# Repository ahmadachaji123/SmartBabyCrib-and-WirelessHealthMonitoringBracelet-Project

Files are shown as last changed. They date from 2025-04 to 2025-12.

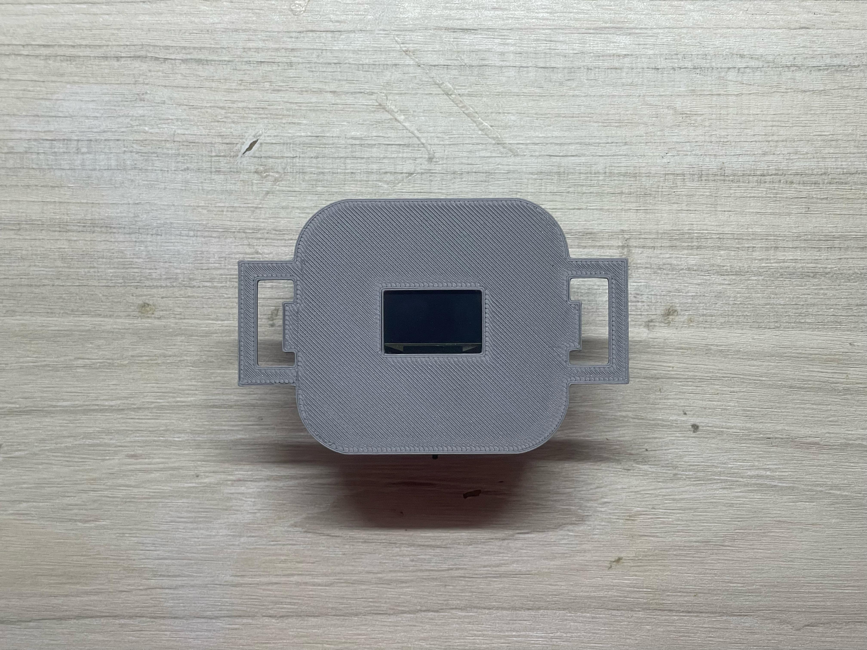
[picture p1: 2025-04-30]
Photo/design.jpg

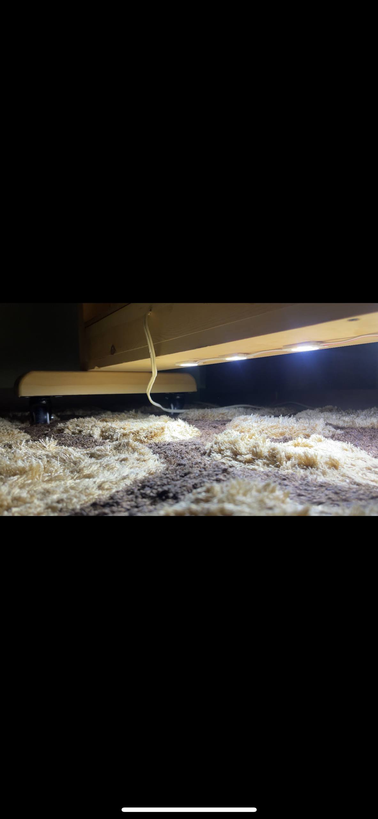
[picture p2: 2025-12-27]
Photo/photo_2025-12-27_20-52-59.jpg

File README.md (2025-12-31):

Smart Baby Crib – Final Year Project
A fully integrated Smart Baby Crib System developed as a Final Year Project in Mechatronics Engineering, focusing on baby safety, health monitoring, automation, and remote access.

🔹 Features
Wireless Health Monitoring: Heart rate, body temperature, and SpO₂ displayed on crib screen and mobile app
System Status: Bracelet battery, ambient temperature; humidity fixed at 70% (sensor damaged)
Remote Monitoring & Control: Mobile app connected via Wi-Fi to an online database, full control from anywhere
Synchronized Control: Swing, lights, music, system status updated in real time between crib and app
Auto Mode: Can be enabled/disabled from crib or phone; currently triggered by noise, planned upgrade to baby-cry detection
Health Data Visualization: 7-day real-time graphs (HR, temperature, SpO₂) on app or web browser; older data deleted automatically

🛠 Technologies
Embedded C/C++ for microcontrollers
Wireless sensors and communication modules
Mobile app & web dashboard for control and visualization
Mechanical design & structural analysis

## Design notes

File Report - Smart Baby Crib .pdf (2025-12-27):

1 | P a g e

## RAFIK HARIRI UNIVERSITY

## SMART BABY CRIB

Done by

## AHMAD ACHAJI

## AHMAD HAMMOUDEH

## SLEIMAN SMAILI

## ZIAD ZOK

Submitted to

## DR. Ahmad Koubeissi

This Senior Project is submitted in Partial Fulfillment of the Requirements of the BE Degree of

Mechatronics Engineering Major of the College of Engineering at Rafik Hariri University

## MECHREF-LEBANON

## April 2025

2 | P a g e

Copyright © 2024. All Rights Reserved

Ahmad Achaji (20210313)

Ahmad Hammoudeh (20210482)

Sleiman Smaili (20210629)

Ziad Zok (20210281)

3 | P a g e

## ACKNOWLEDGMENT

This project is the culmination of countless hours of collaboration, dedication, and a shared commitment to innovation in the development of our Smart Baby Crib. It stands as a reflection of the collective efforts of a passionate and determined team striving to bring technological advancements into the world of infant care.

First and foremost, we would like to express our profound gratitude to Dr. Ahmad Koubeissi, whose unwavering support, insightful feedback, and continuous encouragement were vital throughout every stage of this project. His guidance not only propelled our progress but also helped us maintain focus and purpose from inception to final execution.

We would also like to extend our sincere appreciation to the faculty of the Mechatronics Engineering Department at Rafik Hariri University, whose foundational teaching and support laid the groundwork for our academic and professional development. Their role in shaping our engineering mindset cannot be overstated.

To our friends, who offered both moral support and practical advice during the challenging phases, thank you for your uplifting words and clever solutions that helped us navigate tough situations with confidence.

Finally, and most importantly, we owe our deepest thanks to our families. Their boundless patience, love, and sacrifices, whether emotional, physical, or financial, were the pillars that carried us through this journey. Without their enduring belief in our potential, this achievement would not have been possible.

This Smart Baby Crib project is as much theirs as it is ours.

## ABSTRACT

This report presents the comprehensive design and development of a Smart Baby Crib, an innovative system aimed at enhancing infant care by integrating health monitoring, environmental control, and automated soothing mechanisms. The project scope involves the creation of a multifunctional crib that leverages IoT connectivity, real-time sensing, and embedded systems to ensure the baby’s comfort and safety while offering caregivers convenient remote access and control.

The Smart Baby Crib is equipped with vital health monitoring features, including temperature, heart rate, and oxygen level sensors, all wirelessly transmitted via a wearable bracelet. The system includes both manual and automatic operation modes, with automated rocking, music playback, and lighting control triggered by real-time sound detection and sensor feedback. Additionally, a heating and cooling subsystem is implemented using Peltier cells to regulate mattress temperature, ensuring a consistent sleep environment.

4 | P a g e

This report explores the mechanical, electrical, and embedded software design aspects of the crib, emphasizing safety, affordability, and user-friendliness. The project also addresses challenges related to data privacy, long-term operation, and system reliability, delivering a practical solution for modern-day parenting.

5 | P a g e

## TABLE OF CONTENTS

6 | P a g e
Crib ESP32 Code | 101
Crib Arduino Code | 124
Web Graphs code | 134
Mobile application | 148

LIST OF FIGURES

Figure 1: Cradle-Wise Smart Bassinet | 13
Figure 2: SNOO Smart Sleeper Bassinet | 13
Figure 3:Graco Sense2Snooze Bassinet | 13
Figure 4: 4moms MamaRoo Sleep Bassinet | 13
Figure 5: iteration 1 design | 17
Figure 6: Iteration 2 design | 18
Figure 7: Screw-nut mechanism | 19
Figure 8: Motor bracket and shaft | 19
Figure 9: Von Misses analysis on ABS motor shaft | 20
Figure 10: Displacement analysis on ABS motor shaft | 20
Figure 11: Von Misses analysis on “6061” motor shaft | 20
Figure 12: Displacement analysis on “6061” motor shaft | 20
Figure 13: Von Misses analysis on “A36” motor shaft | 21
Figure 14: Von Misses analysis on “A36” motor shaft | 21
Figure 15:Safety factor analysis on “A36” motor shaft | 21
Figure 16: Strain analysis on “A36” motor shaft | 21
Figure 17: Von Misses analysis on “ABS” Platform | 22
Figure 18: Von Misses analysis on “ABS” Platform | 22
Figure 19: FOS analysis on “ABS” Platform | 22
Figure 20: Strain analysis on “ABS” Platform | 22
Figure 21: Von Misses analysis on “6061” Platform | 23
Figure 22: Dis analysis on “6061” Platform | 23
Figure 23: FOS analysis on “6061” Platform | 23
Figure 24: Strain analysis on “6061” Platform | 23
Figure 25: Meshing gears | 24
Figure 26: Factor of safety analysis | 24
Figure 27: Lower Gear | 24
Figure 28: Lower Gear factor of safety analysis | 24
Figure 29: Crib handle | 25
Figure 30: Crib handle factor of safety analysis | 25
Figure 31: Chassis design | 25
Figure 32: FOS analysis on the chassis | 25
Figure 33: Crib Pin | 26
Figure 34: Factor of safety analysis of the pin | 26
Figure 35: Displacment analysis of the base | 26
Figure 36: FOS analysis of the Base | 26

7 | P a g e

Figure 63: Mobile application- Home Screen-Auto mode is off (two different versions) .... 49

8 | P a g e

LIST OF TABLES

Table 1: Challenges and solutions of smart cribs | 15
Table 2: Material and specifications | 27
Table 3: Voltage Levels and Power Distribution | 32
Table 4: Mechanical safety standards | 51
Table 5: Electrical Safety Standards | 52
Table 6: Communication Standards | 52
Table 7: Constants and boundary conditions | 55

LIST OF EQUATION

Equation 2 TP4056 Charging current change | 29

9 | P a g e

TIME PLAN

Phase | Start Date | End Date

Research, Simulations & Component Selection Feb 20, 2025 Mar 5, 2025

Ordering Components & Structure | Mar 6, 2025 Mar 19, 2025
Conceptual Code & Connectivity Testing | Mar 20, 2025 Apr 2, 2025
System Integration & Functionality Testing | Apr 3, 2025 Apr 16, 2025
Troubleshooting & Finalization | Apr 17, 2025 Apr 30, 2025

10 | P a g e

## CHAPTER 1 INTRODUCTION

### 1.1 Background Information

The evolution of baby monitoring devices and smart cribs reflects significant

technological advancements aimed at enhancing infant safety and parental convenience. This

section delves into the historical context, key innovations, and market trends that have shaped

these technologies.

Historical Evolution

The first baby monitor, the Zenith Radio Nurse, was introduced in 1937. Developed by Eugene

F. McDonald and designed by Isamu Noguchi, this device allowed parents to listen to their

infants remotely, marking a pivotal moment in childcare technology (HelloBaby, n.d.). In 1997,

Cynthia Altenhofen invented the first baby monitor with playback and two-way communication,

enabling parents to record and play soothing messages to their babies (Back Then History, n.d.).

Key Innovations

The 21st century has witnessed the emergence of smart cribs, integrating Internet of Things (IoT)

technology to offer features such as real-time monitoring, automated soothing mechanisms, and

environmental controls. For instance, the SNOO Smart Sleeper, developed by Dr. Harvey Karp,

utilizes responsive technology to mimic womb-like sensations, promoting better sleep for infants

(National Center for Biotechnology Information, 2023). Additional advancements include cry

detection systems and mobile applications for real-time updates and control.

Market Trends

The smart crib market has experienced substantial growth, with projections indicating a rise from

USD 316.6 million in 2023 to approximately USD 641.7 million by 2034, driven by parental

demand for enhanced safety and monitoring (Transparency Market Research, n.d.). Despite these

advancements, challenges persist in affordability, data privacy, and the need for comprehensive,

user-friendly designs that cater to a broader demographic. aimed at enhancing infant safety and

parental convenience.

The first baby monitor, the Zenith Radio Nurse, was introduced in 1937. Developed by Eugene

F. McDonald and designed by Isamu Noguchi, this device allowed parents to listen to their

11 | P a g e

infants remotely, marking a pivotal moment in childcare technology (HelloBaby, n.d.). In 1997,

Cynthia Altenhofen invented the first baby monitor with playback and two-way communication,

enabling parents to record and play soothing messages to their babies (Back Then History, n.d.).

The smart crib market has experienced substantial growth, with projections indicating a rise from

USD 316.6 million in 2023 to approximately USD 641.7 million by 2034, driven by parental

demand for enhanced safety and monitoring (Transparency Market Research, n.d.).

Despite these advancements, challenges persist in affordability, data privacy, and the need for

comprehensive, user-friendly designs that cater to a broader demographic.

### 1.2 Literature Review

Introduction

Automated systems are a prominent focus of modern engineering, aiming to minimize human

interference in various domains. Within this context, Simultaneous Localization and Mapping

(SLAM) systems have been extensively researched, laying the groundwork for numerous

advancements. Similarly, the development of smart cribs has gained traction, combining

mechatronic systems, baby monitoring technologies, and IoT applications to improve childcare.

Historical Development

A comprehensive exploration of relevant aspects reveals numerous dimensions influencing smart

crib design. Historical developments trace back to early innovations in baby monitoring during

the 20th century, when devices transitioned from simple analog systems to modern IoT-based

designs. For instance, the introduction of the Zenith Radio Nurse in 1937 marked the beginning

of remote auditory monitoring, while the 1997 invention of the two-way playback monitor by

Cynthia Altenhofen enhanced interaction between parents and infants. In the 2000s, the rise of

IoT allowed devices to transmit data in real-time, exemplified by products like the SNOO Smart

Sleeper, which integrates automated soothing features and environmental control mechanisms.

This evolution demonstrates a continuous enhancement in functionality, connectivity, and user-

centric design. The first baby monitor, the Zenith Radio Nurse, was introduced in 1937,

developed by Eugene F. McDonald and designed by Isamu Noguchi (HelloBaby, n.d.). In the

2000s, the rise of IoT, popularized by figures like Kevin Ashton, enabled real-time data

12 | P a g e

handling, culminating in sophisticated smart crib solutions like the Snoo Smart Sleeper in the

2010s. Ashton (2009) described IoT as a system where the Internet connects to the physical

world via ubiquitous sensors.

Key Mechanisms and Technologies

Advancements in smart crib design emphasize key mechanisms such as:

- Health Monitoring Sensors: Integration of heartbeat, oxygen, and temperature sensors.
- Cry Detection Systems: Using microphones and machine learning to identify and

respond to infant cries.

- Automated Soothing: Employing actuators for rocking motions.
- IoT-Enabled Connectivity: Real-time monitoring and remote control via mobile

applications.

- Comparative Analysis:

The expanded table compares more products available in the market, showcasing the

strengths and limitations of each alongside the proposed smart crib. This approach

highlights how the proposed crib fills gaps in affordability, features, and usability.

Table 1 below demonstrates how the proposed crib integrates advanced features at an

accessible price point, addressing gaps in affordability and functionality.

13 | P a g e

Table 1: Comparison between different Smart Crib products in the market

The figures below show the products used for the comparison

Figure 1: Cradle-Wise Smart Bassinet | Figure 2: SNOO Smart Sleeper Bassinet
Figure 3:Graco Sense2Snooze Bassinet | Figure 4: 4moms MamaRoo Sleep Bassinet

14 | P a g e

Current Challenges

Despite significant progress, challenges remain in areas such as:

- Real-World Usability: Limited focus on diverse household scenarios.
- Affordability: High costs limit accessibility to affluent families.
- Data Privacy: Concerns over IoT-connected devices storing sensitive information.

By addressing these gaps, the project seeks to combine functionality and accessibility in a

comprehensive smart crib design., aiming to minimize human interference in various domains.

Within this context, Simultaneous Localization and Mapping (SLAM) systems have been

extensively researched, laying the groundwork for numerous advancements. Similarly, the

development of smart cribs has gained traction, combining mechatronic systems, baby

monitoring technologies, and IoT applications to improve childcare.

A comprehensive exploration of relevant aspects and subtopics reveals numerous dimensions

influencing smart crib design. Key considerations include mechanical and electrical design,

actuation systems with Arduino-based control algorithms, health monitoring sensors, and IoT-

enabled real-time data management using platforms like Google Firebase. Further advancements

incorporate cry detection for initiating soothing actions, temperature regulation mechanisms, and

mobile app development for caregiver interaction.

The rise of IoT in the 2000s, popularized by figures like Kevin Ashton, enabled real-time data

handling, culminating in sophisticated smart crib solutions like the Snoo Smart Sleeper in the

2010s. Ashton (2009) described the Internet of Things as a system where the Internet is

connected to the physical world via ubiquitous sensors. Current trends explore AI integration,

aiming for affordable, personalized childcare solutions. Landmark studies by pioneers like Dr.

Harvey Karp emphasize soothing techniques and safe sleep environments. Karp's "5 S's"

method—swaddling, side/stomach position, shushing, swinging, and sucking—has been widely

adopted for calming infants (Healthline, 2019).

Despite significant progress, challenges remain in areas such as real-world usability,

affordability, and privacy. The table below outlines the comparison of current systems and

highlights how our project addresses these challenges:

15 | P a g e

Table 1: Challenges and solutions of smart cribs

The proposed solutions aim to make the smart crib more accessible and secure, enhancing its

appeal and functionality for a broader audience. While existing studies emphasize safety and

automation, debates persist regarding wearable versus non-wearable sensors and balancing cost-

effectiveness with advanced features. By addressing these gaps, this project seeks to combine

functionality and accessibility in a single, comprehensive smart crib design.

### 1.3 Project Motivation

Although smart cribs have evolved substantially, gaps persist in delivering a fully

integrated, user-centric solution. Current designs often focus on isolated features such as

soothing mechanisms or health monitoring, failing to provide holistic systems. Additionally, the

high costs associated with these advanced cribs limit accessibility for middle- to low-income

families. Privacy concerns surrounding IoT-enabled baby monitoring also remain inadequately

addressed.

The motivation behind this project lies in bridging these gaps by developing a versatile and

affordable smart crib solution. By integrating monitoring, soothing, and environmental control

functionalities, this project addresses pressing challenges in real-world usability, cost-

effectiveness, and user data privacy. This endeavor aims to enhance childcare accessibility while

maintaining high standards of safety and comfort.

16 | P a g e

### 1.4 Project Objective

The primary objective of this project is to design and develop an affordable smart crib

that incorporates advanced monitoring, soothing, and environmental control systems. The

proposed crib will integrate features such as heart rate and oxygen monitoring, cry detection,

temperature regulation, and real-time IoT connectivity. Utilizing efficient power management

and adaptive actuation mechanisms, the project strives to balance functionality and cost.

Furthermore, incorporating secure data protocols aims to alleviate privacy concerns while

ensuring reliability and caregiver trust.

This project’s goal is to create a user-friendly and highly functional smart crib, setting a

benchmark in cost-effective childcare technology.

### 1.5 Design Constraints

The design constraints of this smart crib project are categorized as technical and non-

technical.

Technical Constraints:

- Power Efficiency: Actuators and systems must consume minimal power to ensure long

battery life and lower operational costs.

- Weight and Size: The crib’s weight should facilitate easy mobility while maintaining

structural stability.

- Sensor Reliability: Vital signs sensors for heart rate, oxygen, and temperature must

provide accurate, real-time data.

- Communication Protocols: Ensure seamless integration of Wi-Fi and Bluetooth for

stable IoT connectivity.

- Safety: Design mechanisms to shield the baby from moving parts, electrical hazards, and

overheating risks.

17 | P a g e

Non-Technical Constraints:

- Cost-Effectiveness: Affordable materials and manufacturing processes to reduce overall

cost.

- Privacy and Security: Implementation of encryption protocols for safeguarding

caregiver and infant data.

- Environmental Impact: Use of sustainable, eco-friendly materials for mattress covers

and crib walls.

These constraints will guide the design process and ensure the final prototype’s compliance with

both technical excellence and social responsibility.

## CHAPTER 2 DESIGN CONCEPTS

### 2.1 Design Iteration 1

First iteration for an up and down mechanism consists of a custom disk cam mechanism for the up and Down motion. But it has multiple problems, 1 risk of slipping, 2 low reliabilities, 3 can’t lift high weights. The picture below shows the mechanism design.

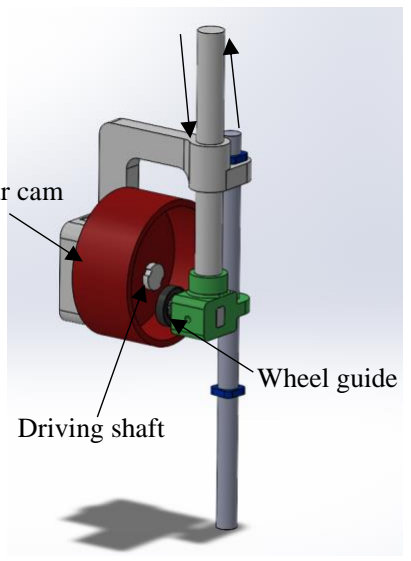
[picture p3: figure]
Driving shaft; Wheel guide

Figure 5: iteration 1 design

Circular cam

18 | P a g e

### 2.2 Design Iteration 2

In the second iteration we tried to create a 4-bar mechanism with guides to create a linear motion in the vertical orientation, the problem in this design is the multiple failure points/ weak points, and no control over the position of the platform due to gravity. The picture below shows the mechanism design.

Figure 6: Iteration 2 design

### 2.3 Design Iteration 3

In the design we have 2 mechanisms, the first one is a standard screw-nut mechanism responsible for the up and down motion, and the other is a simple bracket and shaft for a motor to create a swinging / rocking motion. As shown in the figures below.

19 | P a g e

Figure 7: Screw-nut mechanism

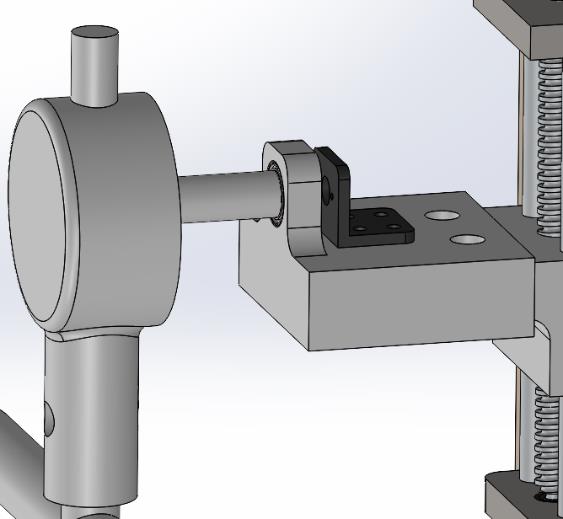
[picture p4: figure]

Figure 8: Motor bracket and shaft

### 2.4 Design 3 Analysis

Analysis:
These mechanisms provide the 2-motion type in the system, and they need to be reliable ensuring smooth motion and safety for the baby. Using SolidWorks analysis we checked the displacement, von misses’ stresses and safety factor, on 3 different materials: 1-ABS, 2- 6061 Aluminum alloy, and 3- A36 Steel.

Motor Shaft
Abs is a widely used plastic used in injection molding and in 3d printing, although the injection molding ABS parts are usually stronger and have 25-30MPA yield strength, 3D printed ABS is weaker due to the imperfections in the printing process and layer adhesion, and due to the layers that are considered weak points and can be snapped if not oriented correctly, so we will assume that 3D Printed ABS has a max yield strength of 15MPA with good quality print and adequate layer position. The figures show analysis of the Motor shaft in ABS.

20 | P a g e

According to von Misses’ analysis the ABS shaft cannot Support the load and undergoes high displacement and eventually yielding.

Like ABS we tried to use 6061 Aluminum alloy and conducted the analysis, but it was also not strong enough and caused failure. The pictures below visualize the analysis of this part using SolidWorks.

Figure 11: Von Misses analysis on “6061” motor shaft

Figure 12: Displacement analysis on “6061” motor shaft

Although displacement is small there are areas of the design that exceeded the max yield strength and can cause failure anytime.

Finally, we Tried A36 Carbon steel and according to the analysis it is suitable and safe to use as a motor shaft, but for more safety it is recommended to change the design of the mechanism to ensure a higher safety factor. The figures show the solid works analysis of the shaft, and Safety factor analysis around the whole design to check if high stresses areas are at risk of failure.

Figure 9: Von Misses analysis on ABS motor shaft

Figure 10: Displacement analysis on ABS motor shaft

21 | P a g e

Figure 13: Von Misses analysis on “A36” motor shaft

Figure 14: Von Misses analysis on “A36” motor shaft

Since the displacement was negligible of less than 0.5mm, and stress was under maximum yield strength by a lot we conducted a Factor of safety analysis to see how much safety factor we have using this A36 carbon steel material as a motor shaft. The figures below show the SF distribution and strain analysis across the shaft.

Figure 15:Safety factor analysis on “A36” motor shaft

Figure 16: Strain analysis on “A36” motor shaft

We can see that in the high stresses area the factor of safety is still acceptable with the lowest value of 3 and higher safety factors across the shaft.

Screw-nut-platform
The screw nut platform is what connecting the whole bed frame into the up and down mechanism and the wooden base, so it must be strong enough with high factor of safety. The figures below show the displacement, factor of safety, Strain and von misses’ analysis of the platform und the full 200n load of the crib.

22 | P a g e

ABS

Figure 17: Von Misses analysis on “ABS” Platform

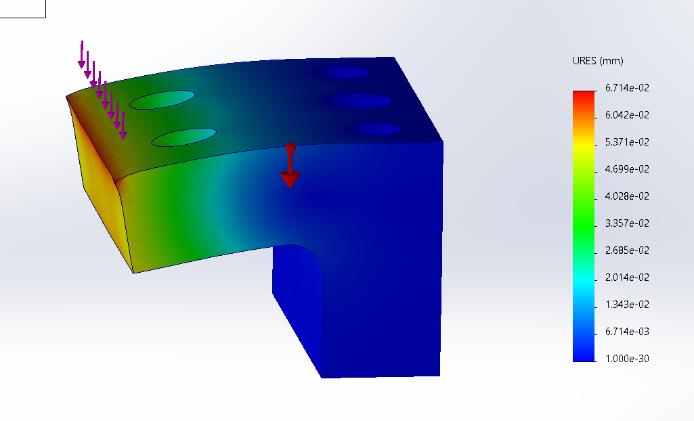
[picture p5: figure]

Figure 18: Von Misses analysis on “ABS” Platform

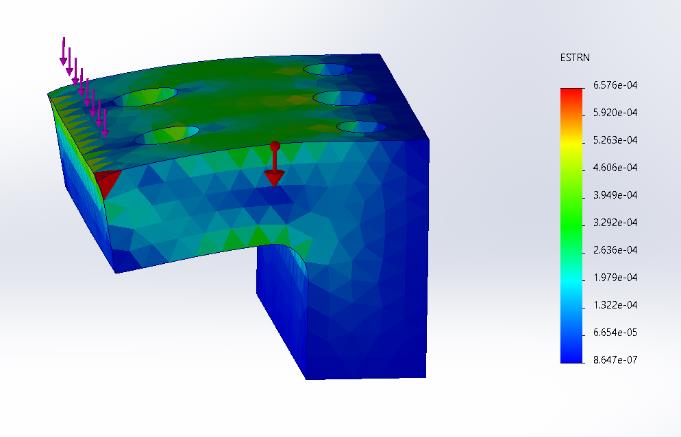
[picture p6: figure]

Figure 19: FOS analysis on “ABS” Platform Figure 20: Strain analysis on “ABS” Platform

The analysis shows that abs are safe enough to use in our design because of the high factor of safety around 10-20 (avg) and very small displacement around 0.0671mm maximum.

6061 ALUMINIUM ALLOY
For increased safety and since this part is moving all the time and needs increased wear resistance we tried to use “6061 Aluminum Alloy” because its easy machine and cheap while maintaining good material properties. The figures below show the analysis in SW.

23 | P a g e

Figure 21: Von Misses analysis on “6061” Platform

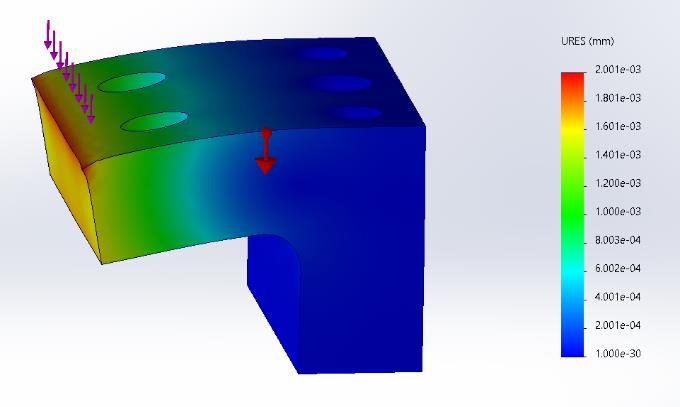
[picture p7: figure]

Figure 22: Dis analysis on “6061” Platform

Figure 23: FOS analysis on “6061” Platform Figure 24: Strain analysis on “6061” Platform

Using Aluminum 6061 instead of ABS increased the minimum factor of safety from 3 to around 9 and decreased the displacement from 0.0671 to 0.00200. So, 6061 aluminum is the better choice for this part.

Design Weaknesses:
In conclusion, although this design is safe to use in the simulated environment, the design practically has 1 critical weak point where all the stress and load are concentrated, which is the shaft part. A suitable solution for this problem is to create a design where the motor shaft is only responsible for rotation and is not under load from the crib’s weight.

### 2.5 Final Design Iteration

Analysis:
Meshing Gears
After running into multiple problems regarding the 2 motion mechanisms we have decided to implement a single motion mechanism. To cut costs and increase durability of the system.

The new mechanism consists of 2 meshing gears driven by a high torque dc motor. The motor shaft is responsible for driving the upper gear. And the lower gear is connected to the crib handles. This gears mesh ensures that the shaft of the motor is not subjected to the weight of the crib therefore less torque required for the crib to start swinging. The figures below show the gear configuration along with some analysis using SolidWorks.

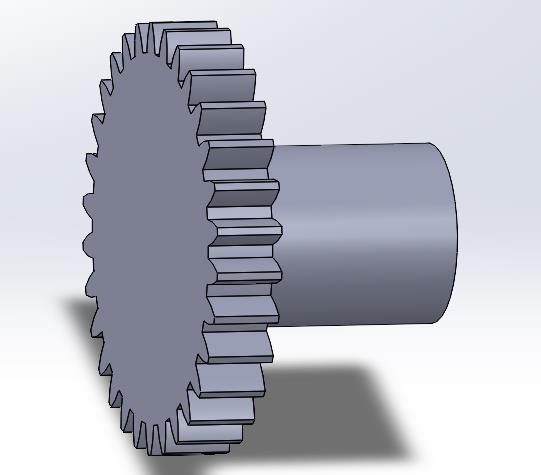
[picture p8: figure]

24 | P a g e
Figure 25: Meshing gears | Figure 26: Factor of safety analysis

The Lower gear is connected from both sides, the first side is connected to the motor shaft, while the other side is connected to the crib handles.

The lower gear is also responsible for holding the weight of the crib from one of the 2 sides

This gear shaft must be strong enough to ensure stable rotation and avoid failures due to the weight of the baby or if one of the parents accidentally leaned on the crib. To make sure no such failures can happen we simulated a 40kg load on the far end of the gear as an extreme scenario. The pictures below show the simulation of the gear using SolidWorks.

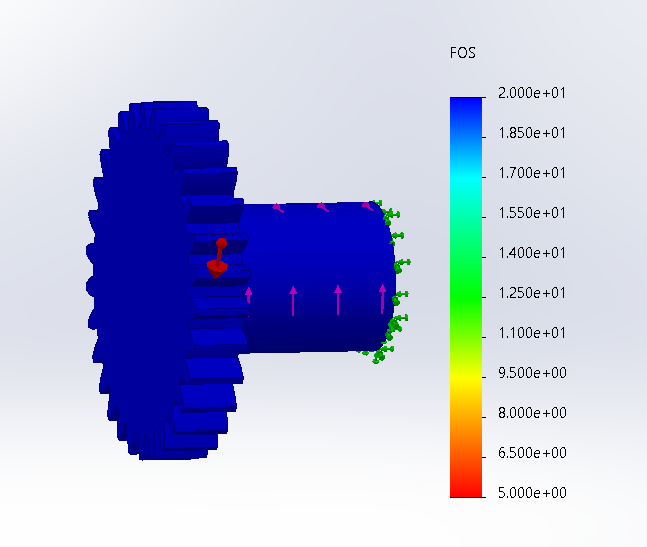
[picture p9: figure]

Figure 27: Lower Gear | Figure 28: Lower Gear factor of safety analysis

Using Cast iron, the gear had a 60 Factor of safety, so we used PLA plastic because it’s lighter, cheaper, quiet, and still withing the safe side having a minimum of 7 Factor of safety.

25 | P a g e

Crib Handles
These handles are responsible for holding the metal chassis. In the pictures below we can see the crib handle along with factor of safety analysis on a 40kg load.

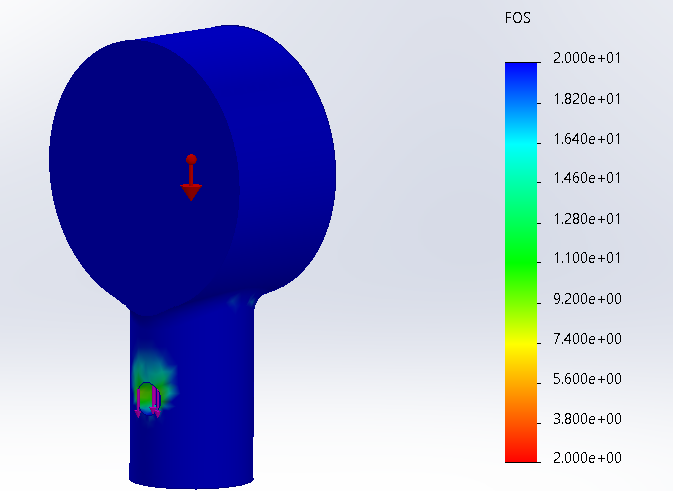
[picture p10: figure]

Figure 29: Crib handle | Figure 30: Crib handle factor of safety analysis

The gear has a minimum factor of safety of 60 if they were made from cast iron. But since the factor of safety is very high and since they are made of cast iron the weight of the piece will add unnecessary load onto the motor. To solve this problem, we were able to print this part using PLA.

Crib chassis
The chassis of the crib was made from cold drawn iron rods with an outer diameter of 23mm and inner diameter of 18mm. The simulation of the crib chassis indicates a minimum factor of safety of 12 times on a 40kg load distributed evenly across the chassis’ bottom as shown in the figures below.
Figure 31: Chassis design | Figure 32: FOS analysis on the chassis

Crib pins
On the other side of the crib, we made a pin responsible for sharing the weight load with the lower gear. And both are placed inside of ball bearings number 6008 2RS to eliminate as much

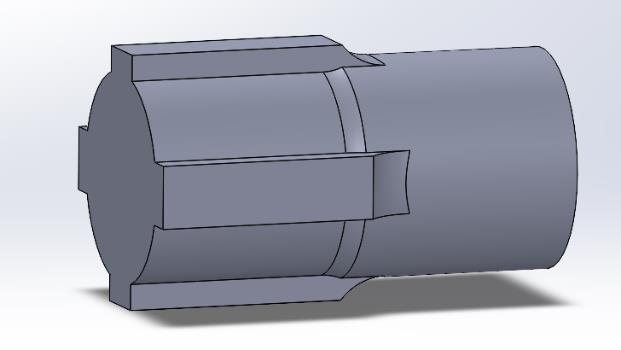
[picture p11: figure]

26 | P a g e

friction as possible and to reduce the load on the motor. The pin is made of PLA and analysis are shown in the figures below.

Figure 33: Crib Pin | Figure 34: Factor of safety analysis of the pin

Crib base
The base of the crib is made of Oak wood and is responsible for the steadiness of the system when swinging. The simulation below shows base’s design under 400N of weight along with the factor of safety analysis. The minimum factor of safety is higher than 100 with a max displacement of 0.0029 mm as shown in the figures below

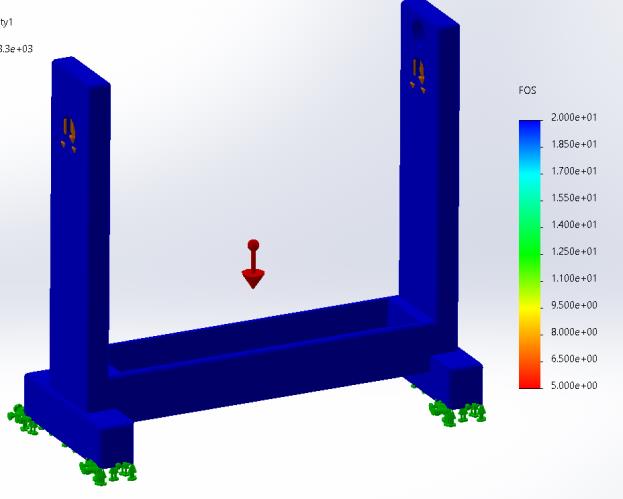
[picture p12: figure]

Figure 35: Displacment analysis of the base | Figure 36: FOS analysis of the Base

In the figure below we can thee the assembly of the crib inside of SolidWorks along with all the forces and constraints that simulate real life conditions.

27 | P a g e

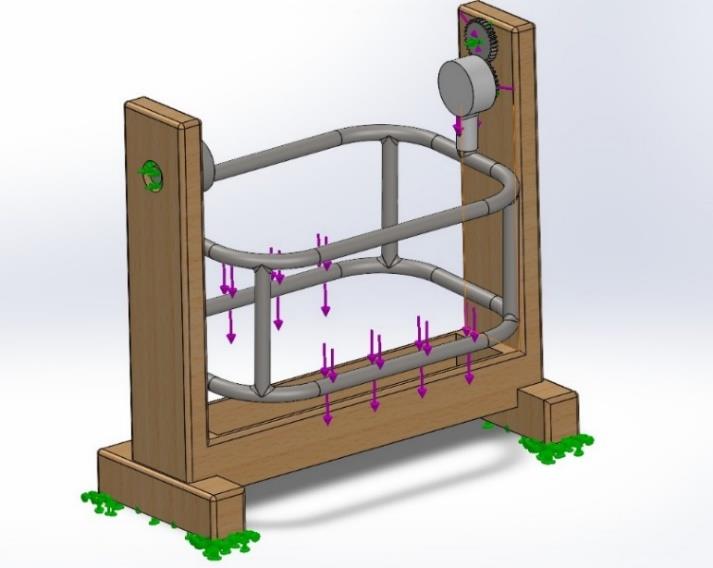
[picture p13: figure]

Figure 37: Assembly Simulation

Implementation
The Base and Chassis are custom made. All Plastic parts were created using the Ender 3 V3 SE 3d printer and ESUN PLA+ plastic filament, with layer lines parallel to the load’s axis to avoid layer separation. The table below shows the exact specification of each pc.

Table 2: Material and specifications

Piece | Material | Specification | Weight
Crib Chassis | Carbon steel | Coated-Painted, against rust | 8Kg
Base | Oak Wood | Sanded | 10Kg
Handles | Brown-PLA+ | 70% infill density with 4 walls layers for extra shock resistance and durability | 700g
Lower Gear | Gray-PLA+ | 70% infill density with 4 walls layers for extra shock resistance and durability | 120g
Motor Gear | Gray-PLA+ | 70% infill density with 4 walls layers for extra shock resistance and durability | 170g
Crib Pin | Gray-PLA+ | 100% infill density for maximum durability and fatigue resistance | 100g

28 | P a g e

Design Discussion:
This final design was able to solve multiple problems, first the motor’s shaft is now separated from the weight supporting shaft and only responsible for rotation. There are no critical points where stresses are concentrated. And the system’s overall safety factor is higher. In the figures below we can see the parts of the project before assembly.

Figure 38: Implemented design

29 | P a g e

MAX30102
MLX90614

## CHAPTER 3 FINAL DESIGN VALIDATION

### 3.1 Technical validation of Final prototype (process)

### 3.1.1 Electric system Schematic

Let us categorize our system into two main subsystems. The first subsystem is responsible for reading the health state of the baby.

For this purpose, we designed a wireless bracelet. For health readings, 2 main sensors are used to measure the heart rate, oxygen rate, and body temperature of the baby; those sensors are the MAX30102 and the MLX90614. Those sensors are compact, precise, and cost-effective, allowing for acceptable reading and monitoring. Figure 39 shows the Two sensors and its position in the bracelet.

Figure 39: Sensors of the Bracelet

An ESP32C3 Mini is used as a main controller. It provides compact size, low power consumption, and wireless communication.

To power the bracelet, a lithium-polymer battery (3.7V 1100mAh) is used with a TP4056 lithium battery charger module. This battery capacity can power the system for up to 6 h. The charger module is set to provide 0.5c of the battery capacity to provide average charging time with long life for the battery, Equation number 2 is used to find the compatible resistor to provide 0.5c. We find that the Rprog value is equal to 1.8kΩ. We implement a voltage divider circuit to determine the battery amount, ensuring that the voltage doesn't exceed 3.3 V. To provide the necessary voltage to the system, the MT3608 step-up module is utilized. It delivers a stable 5V by converting the variable voltage range of 4.2V to 3.3V into 5V. A standard on/off switch is utilized to turn the system on and off. Furthermore, the significance of this switch lies in its ability to ensure that the system does not draw power from the battery while charging. A Resettable Fuse |RXE 160 with 3A value is used to protect the circuit from any short circuit. Important note: the user must not charge the battery and turn on the system simultaneously.

Equation 1 TP4056 Charging current change

30 | P a g e

TP4056
EspC3-mini

Voltage divider

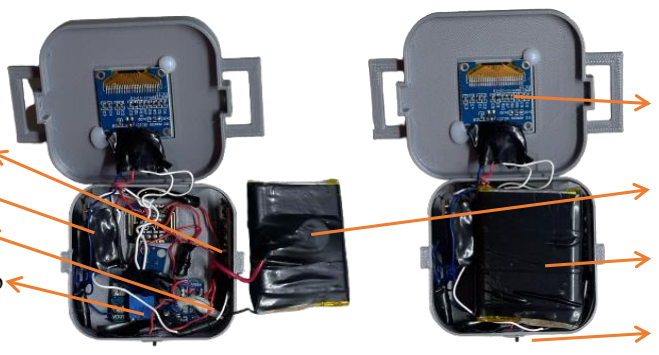
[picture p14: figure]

MT3608 step-up

OLED LCD

lithium-polymer battery

Switch

Resettable Fuse RXE 160

Finally, for visualization, a 0.96" I2C IIC OLED LCD module is used. It is a compact size, and it’s easy to control. All the health data and battery details will occur at the display.to control. All the health data and battery details will occur at the display.

Figure 40 shows the components and their position in the system.

Figure 40: Bracelet components

Figure 41 illustrates the complete connection scheme, highlighting the three categories of the system: sensors/actuators, power, and microcontroller.

Figure 41: Bracelet Electric Schematic

Electrical System Schematic and Power Architecture of the Smart Crib

The electrical system of the smart crib is engineered to balance high-performance actuation, low-voltage embedded control, and electrical safety, all within a unified and efficient architecture.

31 | P a g e

Given the complexity and diversity of the hardware involved, the electrical design was carefully planned to ensure power integrity, voltage regulation, current isolation, and protection mechanisms, particularly because the system operates in close proximity to an infant.

### 1. Power Supply Architecture

At the heart of the crib’s power distribution network is a 240V AC to 12V DC power supply unit. This unit performs the initial AC-DC conversion, transforming the mains voltage into a usable low-voltage DC source. The selection of 12V as the base system voltage is deliberate, as it is high enough to drive electromechanical components like motors, yet still within the safe range for low-voltage electronics.

From this 12V DC source, the power is split and regulated through two primary paths:

High-current 12V Line: Directly powers the Bosch C300 wiper motor via the BTS7960 motor driver. The motor is a high torque brushed DC motor, typically rated for automotive use, and capable of withstanding heavy loads. Since the total load (crib chassis + baby) may exceed 15 kg, the driver must sustain high peak currents. The BTS7960 is well suited for this, offering dual full-bridge drivers with up to 43A peak current capability and internal current sensing features. This line is unregulated in terms of voltage, but all components on this path are rated for 12V operation.

Low-voltage 5V Regulation Line: A DC-DC buck converter steps down the 12V to 5V to supply power to the Arduino controller, rotary encoder, 16x2 I2C LCD, AS5600 encoder, sound sensor, DFPlayer module, relay, and SHT30 sensor. The regulator is chosen with sufficient output current capacity (typically 2A or higher) to prevent voltage drops during peak activity.

Additionally, the Arduino board provides a 3.3V output, which is used to power the ESP32 module. This level shifting is necessary as the ESP32 operates strictly at 3.3V logic levels and is not tolerant to 5V.

### 2. Electrical Safety and Protection

Given the involvement of mains electricity (240V AC) and vulnerable end-users, the system integrates essential electrical safety features:

Circuit Breaker (Disjoncteur): Positioned before the AC-DC power supply, this breaker acts as a first line of defense. In the event of a short circuit, overload, or insulation fault, the disjoncteur will interrupt the electrical supply, preventing fire hazards, electrical shock, or component damage. Its inclusion is vital, especially in continuous-operation systems installed in domestic environments.

Current Isolation & Grounding: The 240V input and 12V output are electrically isolated via a transformer-based PSU, ensuring that the high-voltage side does not come into contact with the low-voltage logic circuits. Proper grounding and insulation ensure user safety and system stability.

32 | P a g e

Relay Isolation: The LED lighting system under the crib is controlled using a mechanical relay, which provides electrical isolation between the control logic (5V) and the LED power circuit, preventing high current from feeding back into the Arduino in case of a fault.

Table 3: Voltage Levels and Power Distribution

The design considers the maximum current draw of each component. For instance:

The BTS7960 and motor may draw several amps under load — requiring thicker gauge wiring (14–16 AWG) and active cooling if sustained.

The 5V rail supports low-power devices (<100 mA each) but collectively can reach up to 1A or more.

Proper capacitor decoupling and EMI suppression techniques are implemented near sensitive components to minimize ripple and noise from motor switching.

### 4. Electrical Control and Communication Interfaces

The Arduino board acts as the primary control unit, handling logic-level signals, sensor data processing, and user interaction. It communicates with:

I2C Devices: The 16x2 LCD, SHT30 sensor, and AS5600 encoder share the I2C bus for data exchange.

Digital Pins: Used to control the relay, read the rotary encoder pulses, and communicate with the DFPlayer and sound sensor.

ESP32: Powered by the 3.3V line, this module manages wireless functions (e.g., Wi-Fi, Bluetooth) and could eventually support mobile app communication or cloud logging of sensor data.

### 5. Design Considerations for Long-Term Operation

The system is designed for continuous usage, meaning the electrical components must remain stable, cool, and protected during operation. Key considerations include:

- Thermal Management: Heat sinks are mounted on the BTS7960 and step-down regulators to dissipate heat under full load conditions.
- Load Testing: The power system has been tested under full-load scenarios to ensure voltage stability and protection response times.
Voltage Level | Purpose | Powered Components
240V AC | Mains input | Enters PSU for conversion
12V DC | Motor drive and base voltage | Bosch C300 motor, BTS7960 driver
5V DC | Control logic and sensors | Arduino, LCD, DFPlayer, sensors
3.3V DC | Wireless module | ESP32

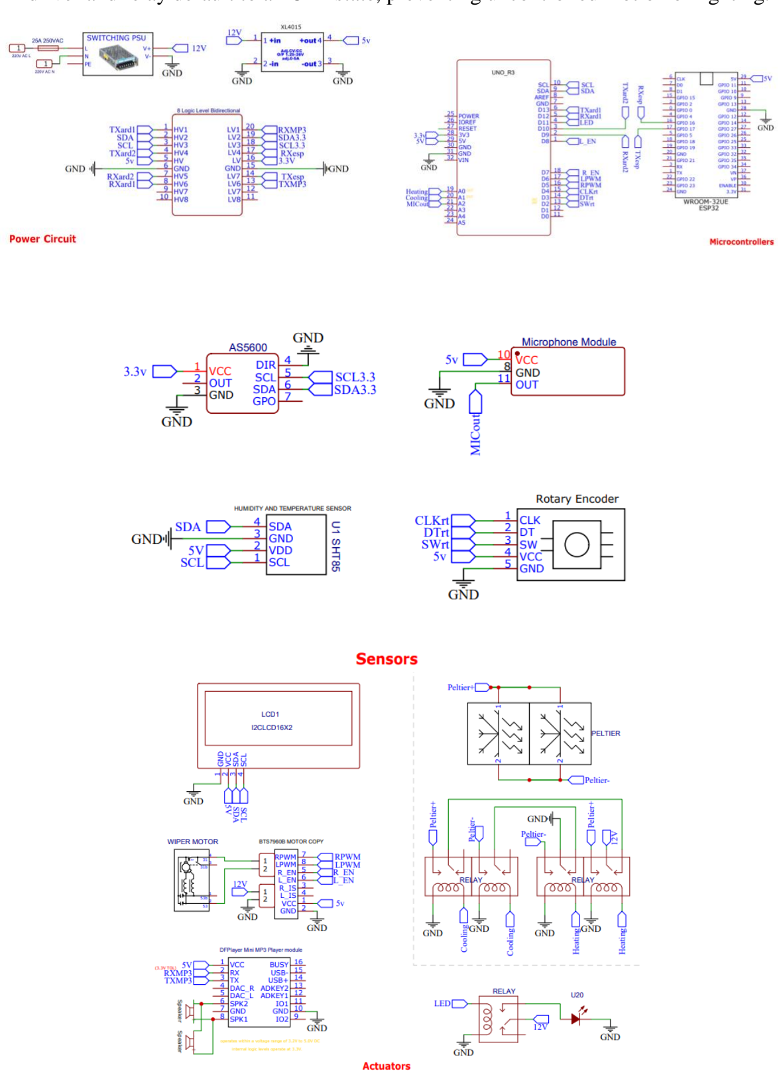
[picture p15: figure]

33 | P a g e
- Fail-Safe Operation: In case of unexpected shutdowns (e.g., power outage), the motor driver and relay default to an OFF state, preventing uncontrolled motion or lighting.

Figure 42: Crib Electric Schematic

34 | P a g e

Figure 43: Electrical system 1

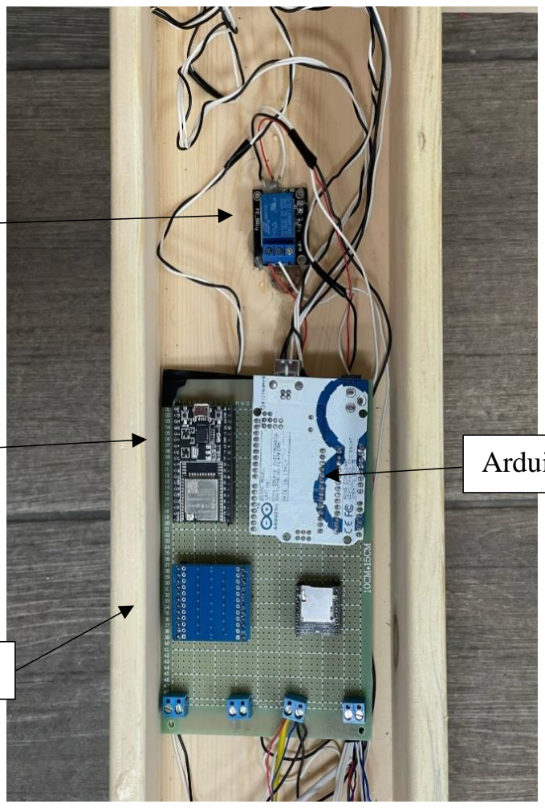
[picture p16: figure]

Figure 44: Electrical system 2

bts7960

Main power supply

Circuit breaker

Motor drive

Arduino UNO

Relay

ESP

Logic shifter

35 | P a g e

Figure 45: Speakers, Mic, and Temp Sensor

Figure 46: HMI and magnetic Encoder

Speaker

Mic

LM75 Temperature Sensor

Magnetic Encoder

LCD screen

Rotary Encoder

36 | P a g e

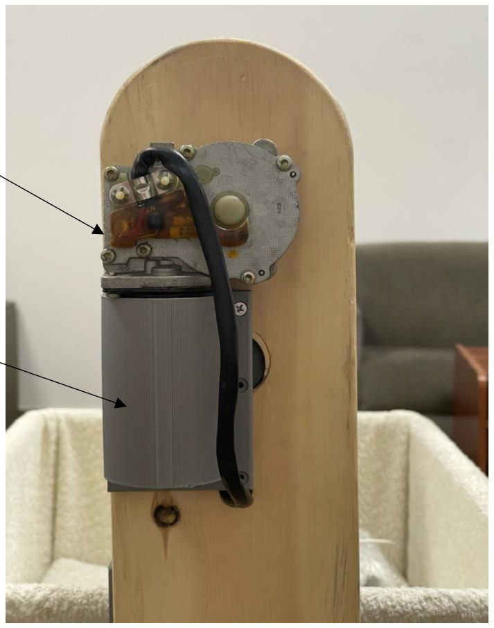
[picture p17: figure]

Figure 47: Motor and bracket

### 3.1.2 Embedded System Communication Architecture

The communication system will be divided into 3 subsystems, made to ensure a robust, flexible, and reliable communication system.

The first subsystem represents communication between the bracelet and the crib system. The aim of this communication is to transmit health data about the baby to the main controller. To do so, the system will start by using the ESP-NOW protocol between the EDS32C3-mini and ESP32-Wriim-32D. This protocol is compatible with our task because it provides direct, peer-to-peer communication without Wi-Fi infrastructure, low latency and fast data transmission, low power consumption (the bracelet is battery-based; the less power consumption, the better), flexible communication topologies, reliability and robustness in congested environments, communication ranges up to 220 meters under ideal conditions or 50–100 meters in typical indoor environments, and easy pairing and device provisioning. This makes ESP-NOW a perfect choice in our scenario.

In our system, we send sensor data from one ESP32 to another using ESP-NOW, and to ensure efficient and reliable transmission, we use a packed structure composed of fixed-size unsigned integer types, specifically uint8_t and uint16_t. These types represent 8-bit and 16-bit unsigned integers, offering predictable and compact data sizes. For example, uint8_t can store values from 0 to 255 using just 1 byte, while uint16_t handles values from 0 to 65,535 using 2 bytes. This

DC Motor

DC Motor
Bracket

37 | P a g e

approach significantly reduces memory usage and transmission overhead compared to using floating-point types. To maintain precision for values like temperature, we multiply them by 10 and store them as integers (e.g., 36.5°C becomes 365). This method avoids floating-point issues and keeps the data structure simple and consistent. Overall, using a packed structure with these types makes the data transmission faster, more memory-efficient, and easier to decode on the receiving ESP32. Figure 48 shows the structure and the type of sensory data 1.

Figure 48: packed structure of the sensory data 1

After receiving the data from the ESP32C3 Mini, the ESP32-WROOM-32D needs to transmit this data to the Arduino (main microcontroller). To do so, a UART protocol is used to provide an easy, robust, and easy-to-implement protocol, especially in the short distances (the ESP32-WROOM-32D is very close to the Arduino).

Figure 49 illustrates the first subsystem communication lines, protocols, the data that is being sent, and their type.

Figure 49: Communication line between bracelet and crib

38 | P a g e

Figure 50 shows how the data in the bracelet and in the crib is synchronized, representing the previous communication line .

Figure 50: Data transmission from bracelet to crib

The second subsystem is the one that connects the Arduino Uno (main microcontroller) to the telephone application; this communication will give the user the access to read and control all the data via the telephone. The Firebase works as a bridge between the mobile app and the crib system; it’s an online database that ensures stability and an easy-to-work environment.

In this subsystem we will have two types of data: readings (sensory, from Arduino to Firebase) and commands (CMD, from mobile to Arduino).

39 | P a g e

Starting with the Readings line, after gathering all the readings of the sensors and the status of the crib (motor mode, light mode, etc.), the Arduino is going to send those sensory data and status data to the ESP32-WROOM. After receiving this data, the ESP32-WROOM is going to send them to the Firebase via Wi-Fi communication, and now the Firebase will save those values. The mobile application will read those values and display them.

Figure 51 illustrates the readings line, their protocol, data type, and root.

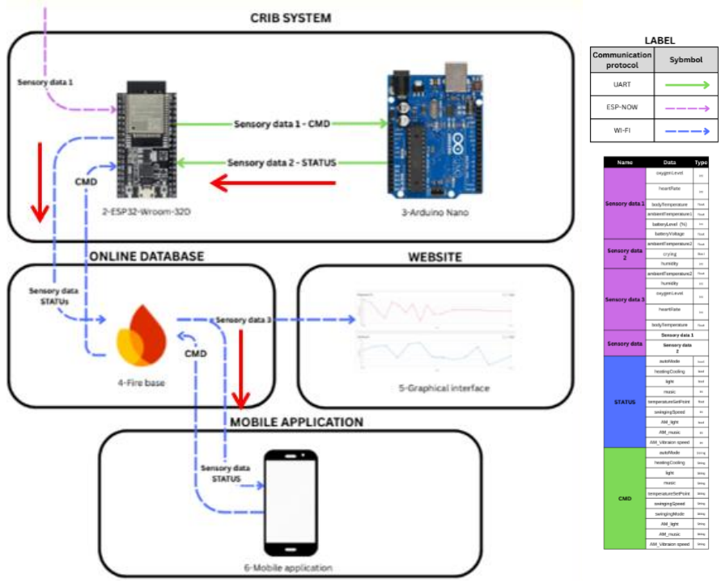
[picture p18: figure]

Figure 51: Reading line communication schematic

Figure 52: Data Base

40 | P a g e

The second line in the second subsystem is the command line; this works exactly in the reverse way of the first line (readings line). The command will appear when the user clicks some button on the mobile app, and this will go to the Firebase. The ESP32 WROOM will read it and send it to the Arduino. The Arduino will take action based on the command.

To avoid problems, a flag variable is used for each command line. This flag will be set to 1 (string) each time a new command occurs. The ESP32-WROOM will check which flag is triggered and send the command to the Arduino and reset the flag after this process. Using the flag method is essential in our system to avoid any possible interlock between some old and new commands and between the main HMI screen and the mobile application.

Figure 53 illustrates the command line, their protocol, data type, and root.

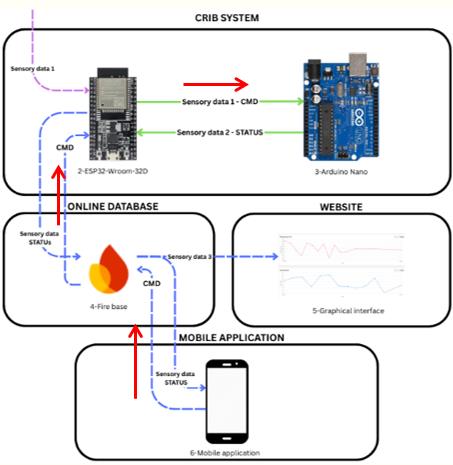
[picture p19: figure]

Figure 53: Command line communication schematic

Figure 54 shows the command variables in the database with their flags.

Figure 54: CMD data in the database

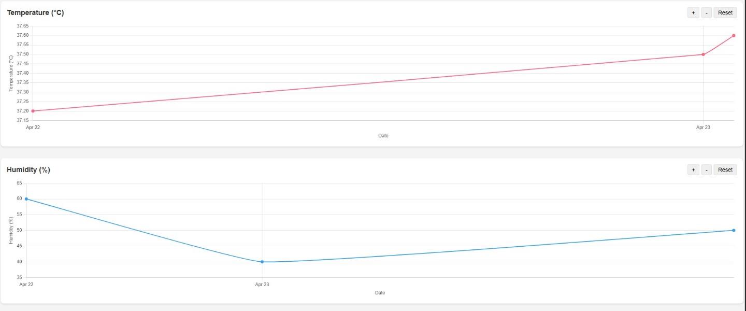
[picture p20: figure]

41 | P a g e

Finally, the third subsystem is a simple, yet effective setup designed to visualize health data using a chart. This subsystem consists of the Firebase Realtime Database and a hosted web server. The web page reads values such as body temperature, humidity, heart rate, and blood oxygen level (SpO₂), and displays them in a dynamic chart with respect to time and date. The chart shows data from the last seven days, and any older entries are automatically deleted to maintain a clean and manageable database. To accurately timestamp each reading, the ESP32-WROOM module utilizes an NTP (Network Time Protocol) library to retrieve real-time data. It then attaches the corresponding timestamp to each reading before sending it to Firebase.

Figure 55 shows the web page that contains the graph

Figure 55: Graphs of the health condition of the baby

Figure 56 shows the timed data and how they are categorized in the database.

42 | P a g e

Figure 56: shows the timed data format and path in the firebase

Figure 57 shows the summary schematic of the Embedded System Communication Architecture with the communication protocol, data transferred with its type.

Figure 57: Full communication Architecture

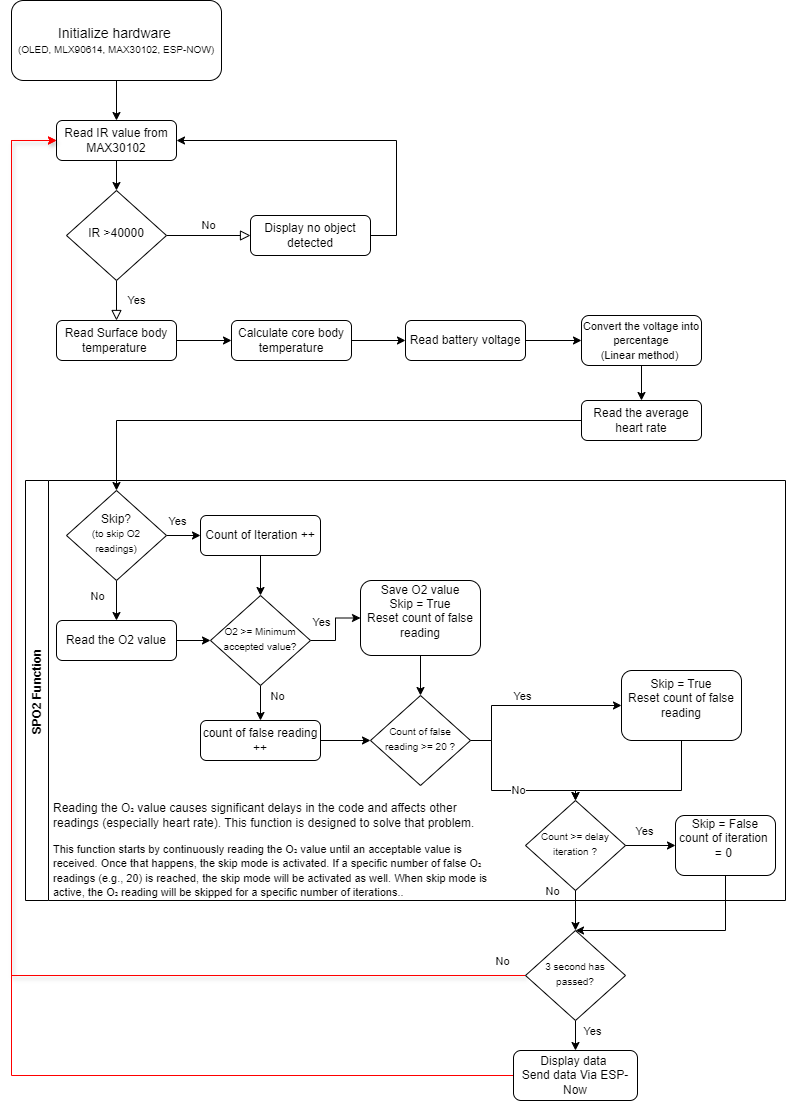
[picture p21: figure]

43 | P a g e

### 3.1.3 Mode of operation

Bracelet
The main aim of the bracelet is to read and transmit those readings to the main controller. To do so, the algorithm is straightforward; it follows the following order: reading sensory values, printing them, and sending them via ESP-NOW. Figure 58 represents a flow chart that shows the full operation of the bracelet.

Figure 58: Bracelet algorithm flow chart

44 | P a g e

To start the readings and the entire operation, the baby shall put the bracelet on his hand. When the MAX30102 IR readings become less than 40000, that means that the baby is putting the bracelet on, and he is close enough to start the readings. : Bracelet- no object detected screen, represents the screen that will occur when the the reading of IR sensor is more then 40000.

Figure 59: Bracelet- no object detected screen

There are two types of data in our system: one that’s fast reading and others that are long ones. Those long ones need to take a lot of samples to start giving an output.

Starting with the fast readings system, first, the system will read the surface skin temperature of the baby using the MLX90614 sensor. To calculate the internal body temperature, a linear calibration curve is implemented based on the ambient and surface body of the baby (to get more reliable readings, we can edit at the calibration curve and apply more testing).

The user shall be notified about the battery level all the time; to do so, the system will now read the average voltage value of the battery and multiply it by the value of the voltage divider circuit. A linear conversion is applied to change this voltage into a percentage; 3.3 V represents 0%, and 4.2 V represents 100%. One important note is that the battery voltage is actually not linear, but we are going to use a linear curve for simplicity.

Going to the next type of reading, which is the slow readings, the system will start to take the required samples of the heart rate, but without applying any while loops or delays. But one major problem in the system is that the SpO2 readings and the heart rate readings affect each other, and we can’t get the two values together. We won’t see any heart rate values until SpO2 has a value.

The SpO2 contains a lot of loops that are built in its library, leading to delaying the system too much. That’s why we let the SpO2 readings happen once every specific number of iterations. This method can help to stabilize the system and will let us get the HR values. There is some filtration happening at the HR, and the SpO2 values—every value that is below 40 or 90 will be rejected.

45 | P a g e

After finishing the readings, now we are going to check if three seconds have passed or not using the Millis function. If yes, we are going to present the health readings at the OLED display. readings Shows the values of all the readings at the screen.

Figure 60: Bracelet- screen readings

After printing them, we now need to prepare to send them via ESP-Now. To do so, we are going to fill our structure value with the required data and in the right type. The data that we are going to send will be of the Unit type, so the integer readings will stay the same and the float values will be multiplied by 10 if uint_8 or 100 if uint16 (higher accuracy). This step is important to convert the float value into an integer; the value will be converted back into the received microcontroller. : Transmitted data from bracelet to esp32 Via Esp-now Shows how the data is being transferred to the main controller using ESP-now protocol.

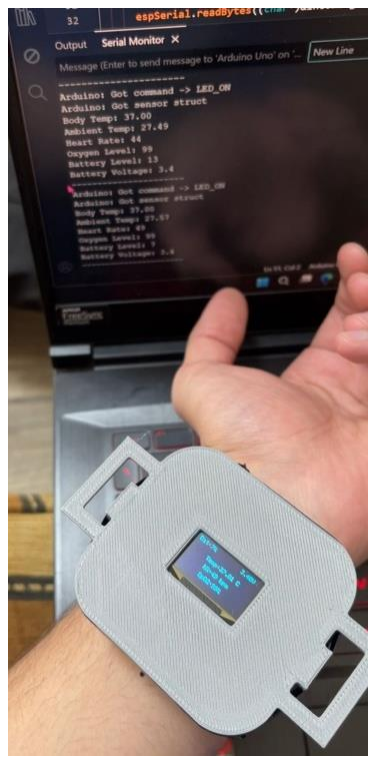
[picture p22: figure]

Figure 61: Transmitted data from bracelet to esp32 Via Esp-now

46 | P a g e

Now we are going to start the loop again and repeat all the previous steps.

Important Considerations: The SpO2 and heart rate readings are not so accurate, but comparing the accuracy with the cost, they are pretty good and compatible with the system. The heart rate readings need close to 1 minute to start giving good value, and it accumulates until it reaches the correct value.

Now let’s talk about the algorithm and how our crib will function:
First, as a user, we will only be controlling the crib and reading the value from sensors using the lcd and rotary encoder, so let see the interface of the lcd screen step by step.

We will start by O2 Level this value will be taken from the bracelet and passed it on the screen not only O2 level but also Heart rate, Body temperature, ambient temperature and battery level all these value will be appear on the screen and even if the bracelet is turn off it will still print the last value of the sensor, this step is made as safety mode so if for example the heart rate are abnormal and the mother didn’t recognize this when she will come back and check the screen it will take into consideration this point.

Now what about the crying status of the babe, to do so we first try to integrate an ai that detect the crying phase of a baby from other noise but unfortunately we can’t implement this on an Arduino UNO so the solution what to adjust the code so we can approach as much to the crying phase of a babe and we give it a delay so the value on the screen will change only after 30 sec to not affect the screen brightness and control.

Finally for the sensor and reading we also have temperature and humidity sensor near speaker and mic, so he takes this value and print it also on the screen

Now the real important part actuators:
In our crib we have a manual mode and an auto mode we will talk first about the manual mode:

Manual Mode:
The user can control four things in the crib:
- Motor: when the user press on the motor on the menu items, screen will disappear and we will go into a new page called options screen in this screen the user will be able to turn on or off the motor, so if the motor is on when he press on motor and go to the options screen he will be able to turn off the motor and vice versa, and if the user go the options screen by mistake he can press a long press on the push button for 1.5 s and it will go back to the main screen .When the motor is turn on he will move for a specific angle ±3 degrees with a constant speed and he will only be off when the user press on turn off. If you are asking how a dc motor will know that he rotates 3 degrees, now it’s the time to explain about the magnetic encoder. A magnetic encoder is a type of position sensor that detects rotational position, speed, or direction of a shaft using a magnetic field instead of physical contact or optics, so like this when the motor rotate 3 degrees the magnetic will rotate 3 degrees and like this the encoder send data to Arduino to stop the

47 | P a g e

motor and reverse it to the next side, and when we turn off he motor he will go back to the initial position (middle of the crib).

- Light: when the user press on the light on the menu items, screen will disappear and we will go into a new page called options screen in this screen the user will be able to turn on or off the light, so if the light is on when he press on light and go to the options screen he will be able to turn off the light and vice versa, and if the user go the options screen by mistake he can press a long press on the push button for 1.5 s and it will go back to the main screen. The light is controlled by a relay connected to Arduino.
- Music: when the user press on the music on the menu items, screen will disappear and we will go into a new page called options screen in this screen the user will be able to choose the song he wants, we upload 3 songs on our Arduino he can choose which one to play by rotating the encoder and press on the track, the song will repeat till the user enter again to the music go to the final option which will be turn off song, and if the user go the options screen by mistake he can press a long press on the push button for 1.5 s and it will go back to the main screen, but how when upload music to the Arduino without having an mp3 audio, you can play music using tone() on a buzzer or speaker connected to a digital pin. In our code we did so we use melody array to put full tone of a certain music so we can hear tones and not music because Arduino has a short memory.
- Heating/cooling: When the user presses on the heating and cooling on the menu items, the screen will disappear, and we will go into a new page called options screen in this screen the user will be able to choose if he wants to cool the bed or to heat the bed of the babe. When we did so used Peltier cells connected to 4 relays connected to Arduino and for safety, we put a value where the relay should turn off for both cooling and heating.

Auto mode:

When the user press on auto mode screen will disappear and we will go into a new page called options screen in this screen the user will be able to turn on or off the auto mode. When auto mode is activate the system will be looking into the crying status if the babe cry the motor and music will be turn on for exactly 1 min even if the condition back to babe is calm, and for the music the system will choose randomly one of track or the user can a adjust it so he can choose what to play in auto mode.

### 3.1.4 Mobile application

To build the mobile application, the MIT App Inventor is used, a block-based mobile application creator. The power of the MIT App Inventor is that it gives the user the ability to categorize the entire mobile application. This website provides all the necessary components, from buttons and layers to text colors and all the logic needed. The advantage of this website is that there is a built-in function for Firebase, which will facilitate the process and make it easier; moreover, it can let the user upload a full webpage inside it. Those features make the MIT app very suitable for our project. The main drawbacks of this application are that it works only in the Android system.

48 | P a g e

Figure 62: shows the Mobile app icon.

The system will include a mobile application that enables users to monitor and control the Crib via Wi-Fi, as previously mentioned. The app will display real-time sensor readings, crib status, active modes, and actuator operations, providing comprehensive oversight. The user interface consists of four intuitive screens for seamless navigation. Figure 63 shows the different available screens in the mobile application.

Figure 63: mobile application screens

Screen 1: Home Screen

This serves as the central dashboard, allowing users to view all vital baby data (e.g., health metrics) and crib status briefly. From here, parents can also control the crib’s functionalities, such as activating or deactivating heating/cooling, swinging, and the light system. Moreover, the user can set the temperature set point and the swinging speed. And he can switch between music. He can see a live demonstration about what is happening in the system and whether the
command that he sends is activated or not.

The home screen control will be locked when the auto mode is activated. The user can only control the cooling and heating system because it’s not included in the auto mode.

As illustrated in Figure 64, the home screen presents the baby’s health status alongside the crib’s operational state. Visual indicators, such as color-changing push buttons and dynamic icons, provide immediate feedback on the crib’s current mode and active actuators.

49 | P a g e

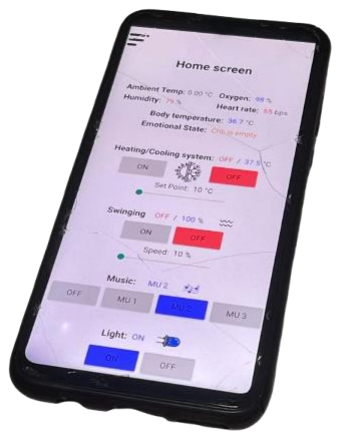
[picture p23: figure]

Figure 64: Mobile application- Home Screen-Auto mode is off (two different versions)

Figure 65 illustrates the home screen when the auto mode is activated.

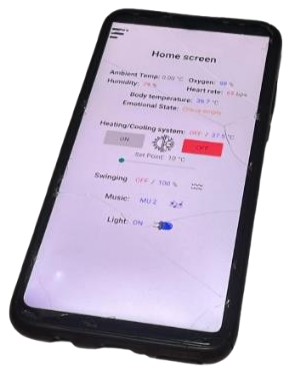
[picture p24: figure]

Figure 65: Mobile application- Home screen- auto mode is ON

Screen 2: Auto mode screen

This screen allows the user either to activate or deactivate the auto mode and set it’s value plus checking the values available in the system. The user can’t change the auto mode parameter if the auto mode is not activated.

Figure 66 shows the auto mode screen in on and off mode.

50 | P a g e

Figure 66: Mobile application- Auto mode screen- auto mode ON/OFF

Screen 3: Graphs screen

This screen shows a web page. This web page shows the graphs of the body temperature, humidity, heart rate, and oxygen rate of the baby for the last seven days. This website is created using JavaScript and is hosted by GitHub. The user can reach those graphs not only from the phone but from any search engine. Those graphs give the user the access to check each point of data and see when exactly it appears.

Figure 67 shows the graphs screen.

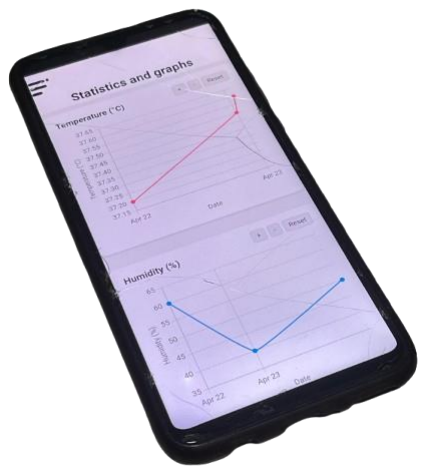
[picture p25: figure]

Figure 67: Mobile application- Graphs screen

51 | P a g e

Screen 3: Live stream screen

This screen is empty for now and it will be for future work , but the main aim of it was to see a live video stream of the baby. Figure 68 illustrates this screen.

Figure 68: Mobile application- Live stream screen

The mobile application code is fully developed and functional. However, the corresponding code on the ESP32 and Arduino side is still under development. As of now, the user can control a few features of the crib via the mobile app, and sensory values are successfully transmitted and displayed. However, the system does not yet support reading or displaying the full operational status of the crib.

### 3.1.5 Safety & Codes and standers

To ensure the safety, reliability, and robustness of the Smart Baby Crib, the design has been reviewed against internationally recognized standards. The following table summarizes the relevant mechanical, electrical, and communication standards, along with how each has been considered or applied in the current system.

### 1. Mechanical Safety Standards

Table 4: Mechanical safety standards

Standard | Title | Application in Project
ASTM F1169-19 | Standard Consumer Safety Specification for Full-Size Baby Cribs | Ensured safe slat spacing, no sharp edges, and stable mattress support. Physical structure is designed to prevent entrapment and collapse.
ISO 7175-1:2019 | Children's Furniture – Beds and Cots – Safety Requirements | Used as a guideline to prevent hazards such as head/limb entrapment, tip-over risks, and mechanical pinch points.
EN 716-1:2017 + A1:2019 | Children’s Cots – Safety Requirements (EU) | Referenced for structural durability, safe locking mechanisms, and compliant dimensions, especially relevant to the crib's swinging feature.

52 | P a g e

### 2. Electrical Safety Standards

Table 5: Electrical Safety Standards

### 3. Communication Standards

Table 6: Communication Standards

## CHAPTER 4 Heating and Cooling

Preliminary Design and Idea Formulation
This project’s initial idea was to improve baby comfort during sleep by maintaining optimal temperature control. Our focus was on developing a system that could provide both heating and cooling to always ensure the baby sleeps comfortably.

The first step in the design process was the selection of the baby bed and mattress dimensions. These measurements were very important for the design of the system components thermal regulation system for the baby bed and mattress.

Standard | Title | Application in Project
IEC 62368-1:2020 | Audio/Video and ICT Equipment – Safety Requirements | The system uses low-voltage (3.3V/5V) components. Protection against overcurrent and overheating has been implemented, with components enclosed in a non-conductive casing.
IEC 60335-1:2020 | Household Electrical Appliances – General Requirements | Motorized swinging system and electronic circuits are isolated, with secure wiring and safe shutdown behavior in the event of a power failure.
EN 62115:2020 | Electric Toys – Safety | Sound output levels are kept below 80 dB for infant safety. All electronic components are shielded and inaccessible to the child. Lighting effects are soft and non-flickering.
Standard | Title | Application in Project
IEEE 802.11 | Wireless LAN (Wi-Fi) Standards | The ESP32 microcontroller communicates with Firebase using a secure 2.4 GHz Wi-Fi connection, protected with WPA2 encryption.
IEEE 802.15.4 (optional/future) | Low-Rate Wireless Personal Area Networks (Zigbee, ESP-NOW) | Used when employing ESP-NOW for device-to-device communication. Data packets are small, fast, and encrypted using MAC-based pairing.
ISO/IEC 7498-1:1994 | OSI Network Reference Model | Used as a reference framework to structure communication: Firebase functions at the application layer, ESP32-UART at transport and physical layers.

53 | P a g e

The first proposed solution was to build an air conditioning system for the baby’s mattress. However, this concept was not pursued due to several reasons. The use of a compressor added a considerable amount of noise that could interrupt baby sleep. Furthermore, the cost of manufacture and the complexity of the unit made the design unfeasible for a compact and safe infant bed.

Figure 68: Air conditioning system (package system)

The “Bed Jet-Type Climate System” system is the second proposed solution. As an alternative, we looked at Bed-Jet systems which are marketed as climate control appliances for beds. They consist of a fan and air tubing that blows warm or cool air directly into the bedding. It is less intricate in design than a full air conditioning unit and

Nevertheless, we identified several limitations that made it unsuitable for our project. Although quieter than a compressor, the Bed Jet still produces noticeable noise, particularly at higher fan speeds, which could interfere with a baby’s rest. Moreover, the use of an external air hose posed a potential safety concern when used near infants (A reviewer from The Strategist noted that the Bed-Jet frequently tripped their bedroom’s circuit breaker, requiring regular resets. Although customer service provided a workaround, this indicates potential compatibility issues with certain electrical systems. Additionally, a user on Reddit shared a troubling experience where they received damage), and the presence of moving parts added to the overall system complexity and potential maintenance requirements.

54 | P a g e

Figure 69: Bed-Jet Climate System

In search of a more efficient and baby-friendly alternative, we explored other technologies and ultimately identified Peltier Cell as the most suitable solution. Peltier cells offer a quieter operation, simpler design, lower cost, and safer for the baby, all while meeting the project’s core objective of providing a comfortable sleeping environment for the baby.

So, what are Peltier cells?

Peltier cells, or thermoelectric coolers (TECs), are solid-state heat pumps that heat and cool based on the Peltier effect. When an electric current is passed through the junction of two unlike types of conductors or semiconductors in the cell, one will take up heat and the other release heat. This creates a temperature gradient: one side gets cold (ideal for cooling devices), and the other side gets hot (which may be used for heating or must be dissipated). The direction of heat flow can be reversed by merely reversing the direction of the current, thus one can use the same device as a heater or a cooler. Peltier cells are efficient, light, and compact for local thermal control, and they are well suited to be used in applications including portable coolers, cooling electronic components, and even heated or cooled beds or seats.

55 | P a g e

•

Figure 70:Peltier Cell

System Implementation through Simulation
After selecting Peltier Cells as the optimal solution for temperature regulation in the baby mattress, the next step was to translate this concept into a practical and functional design. To achieve this, we chose to begin with simulation-based development, allowing us to model and analyze the thermal behavior of the system before proceeding to physical implementation. In order to properly distribute the heat along the selected mattress we noticed that using a thin layer of aluminum foil will be helpful. The selection of the mattress dimensions, knowing the constants and boundary conditions, and selecting the number of Peltier cells was the first step to go into the simulation. We used Ansys Workbench as software for the heat transfer simulation.

In the first trial of bed heating simulation, we used the following data:

Table 7: Constants and boundary conditions

Mattress dimensions | Constants and boundary conditions
lengℎt: 70 cm | w kaluminum foil = 210 . k m tℎicknessaluminum foil = 0.2cm
Widtℎ: 45 cm | w kmattress sponge = 0.06 . k m
Tℎickness: 6 cm | Tambient = 17℃ Tinitial = 60℃ w ℎair = 5 . k m

56 | P a g e

In the first trial we used 2 cells under the mattress so the result on the upper surface was about 23℃ which is not suitable for baby warming.

The second simulation trial has some modifications in the mattress thickness (we consider it to be 3 cm). The other data was kept the same as trial 1.

The results of the second trial were acceptable for baby warming (about 29℃). The results are shown below:

Figure 71: Ansys analysis

The results of Ansys give that the temperature at the top surface of the mattress is about 29℃. The research shows that for an adult a temperature between 30 and 35 ℃ is acceptable for heating so for a baby a 28-29 ℃ temperature is compatible.

Physical Prototype and Testing
As the simulation was done, we chose to use 2 Peltier Cells as heating and cooling sources. The mattress dimensions were:

lengℎt: 70 cm

Widtℎ: 45 cm

Tℎickness: 6 cm

To optimize heat transfer, we essentially split the mattress into two thermally identical sections, each measuring 3 cm thick. This arrangement enhances the provision of evenly distributed temperature regulation in the mattress body. The adjoining two sponge layers were sandwiched between a thin layer of aluminum foil (0.1 cm tℎick) to help evenly distribute heat across the contact area with the baby. It chose aluminum for its high thermal conductivity, which helps to dissipate heat evenly and prevents the formation of hot spots. From a safety perspective, too, the

57 | P a g e

aluminum foil is a protective factor. This is triggered in case of any electrical short circuit or power strike, the foil helps to dissipate heat and prevent direct ignition of the surrounding sponge material. This dual-purpose design enhances both the thermal performance and the safety of the mattress, making it suitable for use in infant sleep environments.

The Peltier cells we used were of 12 V input and gave a temperature of 60 ℃ each.

The Cells will be connected directly to the power supply. The figures below will show where and how it is located.

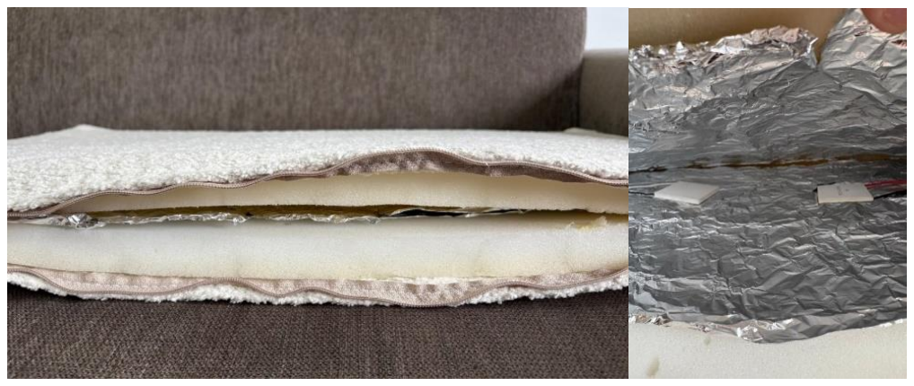
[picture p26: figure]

Figure72: Peltier cells Prototype

## CHAPTER 5 Conclusion & Future work

### 5.1 Future Work: Enhancing Intelligence and Usability

As the Smart Baby Crib continues to evolve, several promising directions have emerged that can significantly enhance its capabilities and user experience. One notable enhancement is the addition of a live streaming system, allowing parents to visually monitor their child in real-time through the mobile application. This feature will not only improve peace of mind but also expand the crib's role as a complete monitoring solution.

Another key improvement involves enhancing sensor accuracy, particularly for health parameters like heart rate and SpO₂ levels. More reliable readings will contribute to better decision-making and ensure the system's effectiveness in critical situations.

The integration of a machine learning model for cry detection presents an exciting step toward intelligent responsiveness. By training an algorithm to distinguish between various types of infant sounds, such as hunger cries versus discomfort cries, the system could take more targeted and appropriate soothing actions. This adaptive intelligence would elevate the crib from a responsive device to a predictive caregiving assistant.

On the user interface front, upgrading to a larger screen on the main system could significantly improve usability and visibility, especially for real-time status updates and manual control. Meanwhile, developing an iOS-compatible version of the mobile application would expand

58 | P a g e

accessibility to a broader range of users, ensuring a seamless experience across all major platforms.

Together, these future upgrades represent an exciting roadmap for turning the Smart Baby Crib into a fully integrated, intelligent, and user-friendly solution for modern parenting.

### 5.2 Conclusion

In summary, this project has detailed the design, implementation, and validation of a Smart Baby Crib—an innovative solution that merges health monitoring, environmental control, and automated care features into one cohesive system. From wireless wearable sensors to IoT-enabled functionalities and a custom mobile app, the crib has been designed to offer both convenience and reliability to caregivers, while prioritizing the comfort and safety of infants.

The development process was marked by continuous iteration and problem-solving, whether in optimizing mechanical structures, managing power distribution, or refining communication protocols. Each design challenge led to a creative solution, ultimately resulting in a working prototype capable of monitoring vital signs, reacting to sound cues, and providing comforting responses through movement, lighting, and music.

This project embodies the spirit of applied mechatronics—bringing together mechanical design, embedded systems, wireless communication, and user interface development. It stands as a testament to what interdisciplinary collaboration and engineering innovation can achieve.

As the baton is passed to future development, the Smart Baby Crib is well-positioned to grow into an even more intelligent and essential tool for modern childcare, combining compassion with technology to meet the needs of both infants and parents in the digital age.

59 | P a g e

References

Back Then History. (n.d.). History of baby monitors. Back Then History. Retrieved from

https://www.backthenhistory.com/articles/the-history-of-baby-monitors

HelloBaby. (n.d.). When were baby monitors invented? HelloBaby. Retrieved from

https://www.hellobaby-monitor.com/blogs/news/when-were-baby-monitors-invented

National Center for Biotechnology Information. (2023). The five "S's" and the "SNOO" Smart

Sleeper—non-pharmacological interventions for infant soothing. National Center for

Biotechnology Information. Retrieved from

https://www.ncbi.nlm.nih.gov/pmc/articles/PMC10485641/

Transparency Market Research. (n.d.). Smart crib market size, industry verticals & overview -

2034. Transparency Market Research. Retrieved from

https://www.transparencymarketresearch.com/smart-crib-market.html

Healthline. (2019). The 5 S's for baby: A guide for soothing your little one. Healthline. Retrieved

from https://www.healthline.com/health/baby/5-s-baby

Ashton, K. (2009). That 'Internet of Things' thing. RFID Journal. Retrieved from

https://www.rfidjournal.com/expert-views/that-internet-of-things-thing

Zulkey, C. (2024, February 20). BedJet Review 2024. The Strategist.

https://nymag.com/strategist/article/bedjet-review.html?utm_source

60 | P a g e

APPENDIX A-Student Outcome
| How was it addressed in your SLP? | Where was it addressed in your SLP?
1. An ability to identify, formulate, and solve complex engineering problems by applying principles of engineering, science, and mathematics
1.1 Identify complex engineering problems | Recognized the need to improve infant safety and sleep quality by automating crib monitoring and environmental control. | Sec. 1.4
1.2 Formulate complex engineering problems | Applied control systems, sensor integration, and embedded system principles to develop a smart crib model. | Sec. 3.1.1, Sec. 3.1.2, Sec. 3.1.3
1.3 Solve complex engineering problems | Solutions incorporated knowledge from courses such as Control Systems, | Sec. 3.1.1, Sec. 3.1.2

61 | P a g e
| Embedded Systems, and Mechatronics.
2. An ability to apply engineering design to produce solutions that meet specified needs
2.1 Design a system to meet specific needs | Designed a baby crib with features that enhance safety, comfort, and usability, considering real-world constraints. | Sec. 1.5, Ch.3
2.2 Modify a system to meet specific needs | Modified sensor layout and control logic after initial testing to optimize performance. | Sec. 3.1.1
3. An ability to communicate effectively with a range of audiences
3.1 Write a formal report | Developed a comprehensive technical report covering all stages of the project from | SLP1 Report (December 10 2024) + SLP2 Final Report (May 29 2025)

62 | P a g e
| planning to testing.
3.2 Deliver a formal presentation | Delivered progress presentations during SLP1 and SLP2 to faculty and peers. | SLPI weekly meetings + SLPII Progress meetings (April 10 2025) + SLPII final presentation (April 24 2025)
4. An ability to recognize ethical and professional responsibilities and make informed judgments
4.1 Consider ethical impact | Considered infant safety and privacy concerns in system design; followed safety standards. | Sec. 3.1.5, Sec. 1.5
4.2 Apply engineering standards and codes | Used standards like IEEE and ISO guidelines where applicable (e.g., sensor use, electrical safety). | Sec. 3.1.5
5. An ability to function effectively on a team

63 | P a g e
5.1 Plan and organize team tasks | Gantt chart and minutes document planning, task allocation, and deadline tracking. | Appendix-C (Meeting Minutes) + Gantt chart in time plan
5.2 Carry out tasks assigned by team | Individual responsibilities were met as outlined in team role assignments and weekly logs. | Progress of the project as illustrated in Gantt chart in time plan + Appendix C (Meeting Minutes)
6. An ability to develop and conduct appropriate experimentation, analyze and interpret data
6.1 Design experiments | Designed experiments to test sensor accuracy, environmental monitoring, actuation and motor response. | Sec. 3.1.1, Ch. 4,
6.2 Conduct experiments | Performed real-time testing in various conditions; data collected from | Sec. 2.5, Sec. 3.1.3, Sec. 3.1.4

64 | P a g e
| sensors and microcontroller.
6.3 Draw evidence-based conclusions | Interpreted sensor data and performance metrics to validate system functionality. | Sec. 3.1.1, Sec. 3.1.3
7. An ability to acquire and apply new knowledge as needed
7.1 Identify necessary skills/tools | Required learning new tools like Arduino IDE, C++, and sensor calibration techniques. | Appendix D (Bracelet ESP32 Code, Crib ESP32 Code, Crib Arduino Code, Web Graphs code )
7.2 Apply self-learned skills/tools | Implemented custom code and control logic for real-time environmental monitoring. | Appendix D (Bracelet ESP32 Code, Crib ESP32 Code, Crib Arduino Code, Web Graphs code )

65 | P a g e

APPENDIX B-Bills of Materials

# MAIN COMPONENTS

COMPONENT | Quantity | total Price

## Store Status

ESP32-WROOM-32U | 1 | $ | robot Pi | Available
| | 9.00 | Shop
SD CARD 2GB | 1 | $
| | 2.00

Available

USB TYPE B MINI | 1 | $
| | 2.00

Available

SHT30-D TEMPERATURE HUMIDITY SENSOR | 1 | $
| | 3.00

Robot
Pi Shop

Available

HIGH SENSITIVITY | 1 | $ | Electros | Available
MICROPHONE SENSOR MODULE | | 3.00
USB 2.0 MINI MICRO SD TF M2
MEMORY CARD READER
1 | $
1.00
Electros | Available
MINI SD CARD MP3 SOUND | 1 | $ | Electros | Available
MODULE | | 4.00
SPEAKER 8 OHM 0.5W | 2 | $
| | 1.20

robot Pi
Shop

Available

WIPER MOTOR 12V (NEW) | 1 | $ | Beb el | Available
| | 30.00 | ramel
BTS7960 MOTOR DRIVER | 1 | $
| | 7.00

robot Pi
Shop

Available

MAGNETIC SENSOR ENCODER | | 1 | $ | Katranji | Available
INDUCTION ANGLE | | 1.50
MEASUREMENT SENSOR |
AS5600
THERMOELECTRIC COOLER
PELTIER 12705 12V 5A CELL
| 2 | $
| | 11.00
Electros | Available
RELAY | Available
ENCODER MODULE | ROTARY | 1 | $
| | 0.90
Katranji | Available
16BY 2 LCD DISPLAY | 1 | $
| | 5.00
Electros | Available
SWITCHING POWER SUPPLY 12V 30A | 1 | $
| | 12.00

robot Pi
Shop

Available

CIRCUIT BREAKER | Available
WIRES THAT CAN HANDLE 20-30
A

Available

8 CHANNEL LOGIC LEVEL | 1 | $ | robot Pi | Available
CONVERTER BI-DIRECTIONAL | | 2.00 | Shop
MODULE
PCB | 1 | $
| | 3.50

robot Pi
Shop

Available

66 | P a g e
40PIN 2.54MM ROUND MALE PIN | 3 | $ | robot Pi | Available
HEADER | | 0.30 | Shop
2.54MM SINGLE ROW FEMALE
1X40 PIN HEADER STRIP BLACK
3 | $
0.99
Electros | Available
CONNECTOR | STRAIGHT | 2 | $ | Katranji | Available
FEMALE PIN HEADER | 40X1 | | | 1.20
3X2.54MM
KF300 2PIN WIRE TERMINAL
COPPER
| 4 | $
| | 1.20

robot Pi
Shop

Available

SOLDER WIRE 0.8MM 50G | 1 | $
| | 2.00
Electros | Available
CP-2515 SOLDERING DESOLDERING WIRE SOLDER WICK | 1 | $
| | 3.00

robot Pi
Shop

Available

1 MM COPPER WIRED BLACK | 6 m | $ | Abou | Available
COLOR | | 2.00 | samra

### 0.5 MM COPPER WIRE BLACK

AND WHITE

6m | $
| 6.00
3 IN ONE WIRE (0.5MM EACH) | 5 m | $ | Abou | Available
| | 1.40 | samra
TINNED COPPER JUMPER WIRE
1M
6 | $
| 0.90

robot Pi
Shop

Available

ESP32-C3 MINI DEVELOPMENT | 1 | $ | Robot | Available
BOARD | | 5.00 | Pi Shop
E-HEALTH SENSOR | OXIMETER
| HEART-RATE | MAX30102
1 | $
1.50
Katranji | Available
MLX90614 NON-CONTACT IR | 1 | $ | Electros | Available
TEMPERATURE SENSOR | | 13.00
0.96" INCH BLUE I2C IIC OLED
LCD MODULE 4PIN
1 | $
4.00
Electros | Available
LITHIUM-POLYMER BATTERY | | 1 | $ | Katranji | Available
3.7V 1100MAH | 50X40X6MM | | 6.00
TP4056 LITHIUM BATTERY
CHARGER MODULE
1 | $
| 2.50

Robot
Pi Shop

Available

RESETTABLE FUSE | RXE 160 | 2 | $ | Katranji | Available
1.6A | | 2.00
RESISTOR CARBON | 2W | 5% |
2K2
2 | $
0.20
Katranji | Available
RESISTOR 1.8K*2 - 1K - 4.7K - | 6 | $ | Robot | Available
1.2K*2 | | 0.30 | Pi Shop
MT3608 2A MAX DC-DC STEP UP
POWER MODULE
1 | $
1.50
Electros | Available
THREE RESISTOR (12K -30K - | 3 | $ | Robot | Available
4.8K) | | 0.15 | Pi Shop
CRIB CONNECTOR (750 G) (20H) | 2 | $
| | 48.00 Available
BIG PIN (40 G) (1.5H) | 3 | $
| | 3.00 Available
ENCODER HOUSING (40G) (2H) | 1 | $
| | 1.50 Available
MOTOR GEAR (140G) (4.5H) | 1 | Available

67 | P a g e
MOTOR STAND (140G) (6.5H) | 1 | $
| | 17.70 Available
SPEAKER HOLDER (100G) (3.5H) | 1 | Available
CRIB HANDLES (40G)(1.5 H) | 2 | Available
SCREEN HOLDER | 1 | $
| | 8.00 Available
SMALL PARTS | -
LOWER GEAR (100G 5.5H) | 1 | $
| | 3.00 Available
BEARINGS 6008-2RS | 3 | $
| | 15.00 Available
BEARING STANDARD 22 MM | 1 | $
| | - Available
METAL CHASSIS | 1 | $
| | 70.00 Available
WOOD AND CRIB INTEGRATION | 1 | $
| | 200.00
201 | Available

$ - تنجيد
| | 80.00 Available

## TOTAL

| VAT | $
| | 1.47
| Shipping | $
| | 37.00
$
637.91

68 | P a g e

APPENDIX C- Meeting Minutes
MINUTES OF MECH 595A MEETING (1)

COLLEGE OF ENGINEERING – MME Department – RHU

Group I

ON SEPTEMBER 24th
, 2025, AT 03:30 PM

Present: Ahmad Hammoudeh- Ahmad Achaji- Ziad Zok- Sleiman Smaili

Absent: none

The meeting came to order at 09:30 am.

### 1. Discussions and Updates

- About the type of mechanism that will be used for soothing up and down motion
- About the smart bracelet device.
- About detecting the presence of the baby in the crib
- About the HMI system
- About the deadline

### 2. Advisor Comments and Recommendations

- Keep 1 mechanism out of the 2 (preferably the swing mechanism)
- Start working on the Human Machine Interface
- Approval on the smart bracelet device.
- Usage of ultrasonic sensors with the up and down mechanism (if used)
- Using the infra-red temperature sensors for (future features)

### 3. Expected Deliverables for Next Meeting

- Simulation for the used mechanism
- Initial control algorithm and components used (sensors/ actuators)
- HMI configuration
- (Bracelet testing)

### 4. Assessment

The meeting was adjourned at 09:48AM.

Minutes taken by: Ahmad Hammoudeh

MINUTES OF MECH 595A MEETING (2)

69 | P a g e

COLLEGE OF ENGINEERING – MME Department – RHU

Group 5

ON January 24th, 2025, AT 09:30 PM

Present: Ahmad Achaji - Ahmad Hammoudeh - Ziad Zok

Absent: Sleiman Smaili

The meeting came to order at 09:30 am.

### 5. Discussions and Updates

- About 1 swinging mechanism instead of two
- About the coupling between the metal gears and the 3d printed part
- About the motor used for the mechanism
- About the bracelet components (How to measure body temperature)
- About the Mobile application

### 6. Advisor Comments and Recommendations

- Using a Bigger battery in the bracelet system
- Calibrating and finding an algorithm to measure the body temperature
- Agreed on the 20 N.m actuator for the swinging mechanism and the feedback on the rotation using a magnetic encoder
- Start printing and fabricating plastic and metal components

### 7. Expected Deliverables for Next Meeting

- Printed part of the mechanism
- Algorithms to measure body temperature
- Entire bracelet algorithm
- Initial crib algorithm + HMI

### 8. Assessment

The meeting was adjourned at 09:33 AM.

Minutes taken by: Ahmad Achaji

70 | P a g e

MINUTES OF MECH 595A MEETING (3)

COLLEGE OF ENGINEERING – MME Department – RHU

Group 5

ON January 24th, 2025, AT 09:30 PM

Present: Ahmad Achaji - Ahmad Hammoudeh - Sleiman Smaili

Absent: Ziad Zok

The meeting came to order at 09:30 am.

### 9. Discussions and Updates

- About the number and configuration of Peltier cells for cooling and heating
- About the swing Motor’s driver
- Testing of the temperature sensor and core temperature algorithm
- About the power supply system
- About the HMI

### 10. Advisor Comments and Recommendations

- Number of Peltier cells required and configuration
- Use of a 45Nm dc motor for swinging
- Agreed on the design and confirmation to the start implementing the system

### 11. Expected Deliverables for Next Meeting

- Printed part of the mechanism
- Entire bracelet algorithm
- Initial crib algorithm + HMI
- Metal and wooden parts

### 12. Assessment

The meeting was adjourned at 10 :00 AM.

Minutes taken by: Ahmad hammoudeh

71 | P a g e

MINUTES OF MECH 595A MEETING (4)

COLLEGE OF ENGINEERING – MME Department – RHU

Group 5

ON February 13th, 2025, AT 09:30 PM

Present: Ahmad Achaji - Ahmad Hammoudeh

Absent: Sleiman Smaili - Ziad Zok

The meeting came to order at 09:30 am.

### 13. Discussions and Updates

- Testing of the wiper motor (speed, direction, and power consumption)

### 14. Advisor Comments and Recommendations

- Changing the motor to another one that can rotate in two directions
- Agreed on the design and confirmation to the start implementing the system

### 15. Expected Deliverables for Next Meeting

- New wiper motor
- Entire bracelet algorithm
- Initial crib algorithm + HMI
- Metal and wooden parts

### 16. Assessment

The meeting was adjourned at 10 :15 AM.

Minutes taken by: Ahmad Achaji

72 | P a g e

MINUTES OF MECH 595A MEETING (5)

COLLEGE OF ENGINEERING – MME Department – RHU

Group 5

ON February 20th, 2025, AT 09:40 PM

Present: Ahmad Achaji - Ahmad Hammoudeh- Ziad Zok

Absent: Sleiman Smaili

The meeting came to order at 09:40 am.

### 17. Discussions and Updates

- Testing the magnetic encoder
- Approval of the metal chassis

### 18. Advisor Comments and Recommendations

- Testing the motor driver and the new motor.
- Testing the screen and touch feature

### 19. Expected Deliverables for Next Meeting

- Entire bracelet algorithm
- Initial crib algorithm + HMI
- Wooden parts

### 20. Assessment

The meeting was adjourned at 10 :05 AM.

Minutes taken by: Ahmad Hammoudeh

73 | P a g e

MINUTES OF MECH 595A MEETING (7)

COLLEGE OF ENGINEERING – MME Department – RHU

Group 5

ON February 27th, 2025, AT 09:30 PM

Present: Ahmad Achaji - Ahmad Hammoudeh

Absent: Sleiman Smaili - Ziad Zok

The meeting came to order at 09:30 am.

### 21. Discussions and Updates

- Bracelet complete algorithm
- Design updates

### 22. Advisor Comments and Recommendations

- Approval of the bracelet algorithm

### 23. Expected Deliverables for Next Meeting

- Initial crib algorithm + HMI
- Completed base and mechanism

### 24. Assessment

The meeting was adjourned at 09:45 AM.

Minutes taken by: Ahmad Achaji

74 | P a g e

MINUTES OF MECH 595A MEETING (8)

COLLEGE OF ENGINEERING – MME Department – RHU

Group 5

ON March 6th, 2025, AT 10:15 PM

Present: Ahmad Achaji - Ahmad Hammoudeh

Absent: Sleiman Smaili - Ziad Zok

The meeting came to order at 10:15 am.

### 25. Discussions and Updates

- Crib structure and mechanical part demonstration

### 26. Advisor Comments and Recommendations

- Approval of the mechanical prototype
- Recommendation to start with merging all the subsystems together

### 27. Expected Deliverables for Next Meeting

- Initial crib algorithm + HMI

### 28. Assessment

The meeting was adjourned at 10:30 AM.

Minutes taken by: Ahmad Hammoudeh

75 | P a g e

MINUTES OF MECH 595A MEETING (9)

COLLEGE OF ENGINEERING – MME Department – RHU

Group 5

ON March 20th, 2025, AT 9:30 PM

Present: Ahmad Achaji - Ahmad Hammoudeh

Absent: Sleiman Smaili - Ziad Zok

The meeting came to order at 9:30 am.

### 29. Discussions and Updates

- Bracelet integration and final design
- System integration

### 30. Advisor Comments and Recommendations

- Designing a PCB design for the bracelet to make it more reliable and robust
- Recommendation to start with merging all the subsystems together

### 31. Expected Deliverables for Next Meeting

- Initial crib algorithm + HMI
- Part of the integrated system

### 32. Assessment

The meeting was adjourned at 9:45 AM.

Minutes taken by: Ahmad Achaji

76 | P a g e

MINUTES OF MECH 595A MEETING (10)

COLLEGE OF ENGINEERING – MME Department – RHU

Group 5

ON March 17th, 2025, AT 9:30 PM

Present: Ahmad Achaji - Ahmad Hammoudeh- Sleiman Smaili- Ziad Zok

Absent:

The meeting came to order at 9:30 am.

### 33. Discussions and Updates

- System integration
- HMI problem
- Final system iteration

### 34. Advisor Comments and Recommendations

- Changing the HMI screen to another one that requires fewer wires
- Managing cables and electrical components in the crib.

### 35. Expected Deliverables for Next Meeting

- A fully functional system that represents the final iteration of the project

### 36. Assessment

The meeting was adjourned at 10:30 AM

Minutes taken by: Ahmad Achaji

77 | P a g e

APPENDIX D-Codes

Bracelet ESP32 Code
#include <Wire.h>

#include <Adafruit_GFX.h>

#include <Adafruit_SSD1306.h>

#include <Adafruit_MLX90614.h>

#include "MAX30105.h"

#include "heartRate.h"

#include "spo2_algorithm.h"

#include <esp_now.h>

#include <WiFi.h>

MAX30105 particleSensor;

#define Battery_adcPin 3

#define SCREEN_WIDTH 128

#define SCREEN_HEIGHT 64

Adafruit_SSD1306 display(SCREEN_WIDTH, SCREEN_HEIGHT, &Wire, -1);

Adafruit_MLX90614 mlx = Adafruit_MLX90614();

struct SensorData {

float ambientTempC;

78 | P a g e

float objectTempC;

float coreTempC; // Calibrated core (axillary) temperature in Celsius

};

/////////////////////////////////////////////////////////////////////////////////////////////////////////////////////

// ADC characteristics

#define VoltageBattery_Calibration 0.71 // the lowest the higher the voltage

const int Battery_adcMaxValue = 4096; // Arduino (1023) - Esp (4096)

const float referenceVoltage = 3.3; // Arduino (5V) - Esp (3.3 v)

//const int numReadings_Battery = 10; // Number of readings for averaging

#define numReadings_Battery 100 // Number of stored readings

// Voltage divider ratio

const float Battery_voltageDividerRatio = 0.25;

// LiPo battery characteristics

const float minBatteryVoltage = 3.0; // Minimum voltage (0% charge)

const float maxBatteryVoltage = 4.2; // Maximum voltage (100% charge)

float voltageReadings[numReadings_Battery] = {0}; // FIFO buffer for voltage values

int currentIndex = 0; // Track the current position in the buffer

int sampleCount = 0; // Counts the number of readings taken

float sumVoltage = 0; // Running sum of stored values

//////insde code variables///////////////////////////////////////////////////////////////////////////////////////////////////

79 | P a g e

int HeartRate = 0;

int32_t O2 = 0;

int batteryLevel = 0;

float batteryVoltage_FV =0 ;

SensorData IR_data;

bool isConnected = false;

int Minimum_accepted_o2 = 90;

int Minimum_accepted_HR = 40;

unsigned long previousMillis = 0; // Store the last time the function was called

/////////////////////////////////////////////////////////////////////////////////////////////////

long irValue = 0;

//presence sensing ////////////////////////////////////////////////////////////////////////////////////

bool presenceState = 0;

//Heart rate///////////////////////////////////////////////////////////////////////////////////////////

bool Startup1 = 0;

const byte RATE_SIZE = 16; // Increased window for averaging

byte rates[RATE_SIZE]; // Array to store heart rate samples

byte rateSpot = 0;

long lastBeat = 0; // Time at which the last beat occurred

80 | P a g e

float beatsPerMinute = 0;

int beatAvg = 0;

// Variables for exponential moving average (low-pass filter)

float filteredBPM = 0;

const float alpha = 0.9; // Smoothing factor (closer to 1 gives smoother, slower response)

//////o2////////////////////////////////////////////////////////////////////////////////////////////////////

bool Startup2 = 0;

int count = 0;

bool skip = 0;

int false_reading_count =0;

#define MAX_BRIGHTNESS 255

#if defined(__AVR_ATmega328P__) || defined(__AVR_ATmega168__)

//Arduino Uno doesn't have enough SRAM to store 100 samples of IR led data and red led data

in 32-bit format

//To solve this problem, 16-bit MSB of the sampled data will be truncated. Samples become 16-

bit data.

uint16_t irBuffer[100]; //infrared LED sensor data

uint16_t redBuffer[100]; //red LED sensor data

#else

uint32_t irBuffer[100]; //infrared LED sensor data

uint32_t redBuffer[100]; //red LED sensor data

#endif

int32_t bufferLength; //data length

81 | P a g e
int32_t spo2; | //SPO2 value
int8_t validSPO2; | //indicator to show if the SPO2 calculation is valid
int32_t heartRate; | //heart rate value

int8_t validHeartRate; //indicator to show if the heart rate calculation is valid

////////////////////////////////////////////////////////////////////////////////

// REPLACE WITH YOUR RECEIVER MAC Address

uint8_t broadcastAddress[] = { 0xe8, 0x6b, 0xea, 0xd4, 0x7b, 0x10 };

// Optimized structure to send data via ESP-NOW that's already compatible with Arduino

typedef struct __attribute__((packed)) {

uint16_t bodyTemp; // Store as integer (value * 100) for 2 decimal places

uint16_t ambientTemp; // Store as integer (value * 100) for 2 decimal places

uint8_t heartRate; // BPM as uint8_t (0-255)

uint8_t oxygenLevel; // SpO2 as uint8_t (0-100%)

uint8_t batteryLevel; // Battery percentage as uint8_t (0-100%)

uint8_t batteryVolt; // Battery voltage * 10 for 1 decimal place

} struct_message;

// Create a struct_message called myData

struct_message myData;

esp_now_peer_info_t peerInfo;

82 | P a g e

// callback when data is sent

void OnDataSent(const uint8_t *mac_addr, esp_now_send_status_t status) {

Serial.print("\r\nLast Packet Send Status:\t");

Serial.println(status == ESP_NOW_SEND_SUCCESS ? "Delivery Success" : "Delivery Fail");

}

void setup() {

Wire.begin(); // for esp32 Wire.begin(SDA,SCL) (9,10)

Serial.begin(11520);

if (!display.begin(SSD1306_SWITCHCAPVCC, 0x3C)) {

Serial.println("OLED initialization failed");

while (1)

;

}

///mlx.writeEmissivity(0.98); // Set emissivity to 0.98 for skin

if (!mlx.begin()) {

Serial.println("Error connecting to MLX sensor. Check wiring.");

while (1)

;

}

Serial.println("MAX30102 Presence Sensing Example");

if (particleSensor.begin(Wire,100000) == false) //Use default I2C port, 100kHz speed

83 | P a g e

{

Serial.println("MAX30102 was not found. Please check wiring/power. ");

while (1)

;

}

WiFi.mode(WIFI_STA);

// Init ESP-NOW

if (esp_now_init() != ESP_OK) {

Serial.println("Error initializing ESP-NOW");

return;

}

// Once ESPNow is successfully Init, we will register for Send CB to

// get the status of Transmitted packet

esp_now_register_send_cb(OnDataSent);

// Register peer

memcpy(peerInfo.peer_addr, broadcastAddress, 6);

peerInfo.channel = 0;

peerInfo.encrypt = false;

// Add peer

84 | P a g e

if (esp_now_add_peer(&peerInfo) != ESP_OK) {

Serial.println("Failed to add peer");

return;

}

particleSensor.setup();

particleSensor.setPulseAmplitudeRed(0x0F); // Increased from 0x0A

particleSensor.setPulseAmplitudeGreen(0); // Turn off green LED

display.clearDisplay();

display.setTextSize(1);

display.setTextColor(SSD1306_WHITE);

display.setCursor(32, 32);

display.print("Hello");

display.display();

}

void loop() {

irValue = particleSensor.getIR();

presenceState = presenceSensing();

if (presenceState) {

IR_data = readSensorData();

batteryVoltage_FV =batteryVoltage_2();

batteryLevel = batteryPercentage_L();

HeartRate = heartRateSensing();

85 | P a g e

O2 = O2_reading_with_delay(2000);

// Serial.print("IR=");

//Serial.print(irValue);

//Serial.print(" Avg BPM=");

//Serial.print(HeartRate);

//Serial.print(" O2=");

//Serial.println(O2);

//Serial.print("Ambient T=");

//Serial.print(IR_data.ambientTempC);

//Serial.print(" Core T=");

//Serial.print(IR_data.coreTempC);

//Serial.println(" *C");

//Serial.print("V | Battery Percentage: ");

//Serial.print(batteryLevel, 1);

///Serial.println("%");

Display_and_send_with_Delay(3000); //sending and displayin data every 3 seconds

}

else {

display.clearDisplay();

display.setTextSize(1.5);

86 | P a g e

display.setTextColor(SSD1306_WHITE);

display.setCursor(10, 32);

display.print("No Object detected");

display.display();

}

}

void Display_and_send_with_Delay(const unsigned long interval) {

unsigned long currentMillis = millis();

if (currentMillis - previousMillis >= interval) {

previousMillis = currentMillis; // Update the last execution time

drawDisplay();

EspNow_sending();

}

}

void drawDisplay() {

display.clearDisplay();

display.setTextSize(1);

display.setTextColor(SSD1306_WHITE);

display.setCursor(0, 0);

display.print("Bat:");

display.print(batteryLevel);

87 | P a g e

display.print("%");

display.setCursor(90, 0);

display.print(batteryVoltage_FV);

display.print("V");

// display.print(isConnected ? "Connected" : "Disconnected");

display.setCursor(30, 20);

display.print("Temp:");

display.print(IR_data.coreTempC);

display.print(" C");

display.setCursor(36, 35);

display.print("HR:");

display.print(HeartRate);

display.print(" bpm");

display.setCursor(37, 50);

display.print("SpO2:");

display.print(O2);

display.print("%");

display.display();

88 | P a g e

}

SensorData readSensorData() { //temperature data

SensorData data;

data.ambientTempC = mlx.readAmbientTempC();

data.objectTempC = mlx.readObjectTempC();

data.coreTempC = calculateCoreTemp(data.objectTempC, data.ambientTempC);

//printIRSensorData(data);

return data;

}

float calculateCoreTemp(float foreheadTemp, float ambientTemp) {

return 0.296 * foreheadTemp - 0.018 * ambientTemp + 28.335;

}

void printIRSensorData(const SensorData &data) {

Serial.print("Ambient = ");

Serial.print(data.ambientTempC);

Serial.print(" *C\tObject (Forehead) = ");

Serial.print(data.objectTempC);

Serial.println(" *C");

// Print the calibrated core temperature in Celsius

89 | P a g e

Serial.print("Calibrated Core (Axillary) Temperature = ");

Serial.print(data.coreTempC);

Serial.println(" *C");

Serial.println();

}

float batteryVoltage_2() {

// Read the ADC value

int adcValue = analogRead(Battery_adcPin);

// Convert to voltage

float measuredVoltage = (adcValue / (float)Battery_adcMaxValue) * referenceVoltage;

float batteryVoltage = measuredVoltage / Battery_voltageDividerRatio;

batteryVoltage /= VoltageBattery_Calibration; // Apply calibration

// Add new value and update the sum

sumVoltage -= voltageReadings[currentIndex]; // Remove the oldest value from the sum

voltageReadings[currentIndex] = batteryVoltage; // Store new reading in FIFO buffer

sumVoltage += batteryVoltage; // Add the new value to the sum

// Move to the next position in a circular manner

currentIndex = (currentIndex + 1) % numReadings_Battery;

90 | P a g e

// Increase sample counter

sampleCount++;

// Compute and return the average only when enough samples are collected

if (sampleCount >= numReadings_Battery) {

float averageVoltage = sumVoltage / numReadings_Battery;

// Debugging output

//Serial.print("ADC: ");

//Serial.print(adcValue);

//Serial.print(" | Raw Voltage: ");

//Serial.print(measuredVoltage, 2);

//Serial.print("V | Smoothed Battery Voltage: ");

//Serial.print(averageVoltage, 2);

//Serial.println("V");

return averageVoltage;

}

return batteryVoltage_FV; // Return -1 to indicate average is not yet ready

}

float batteryVoltage_1() {

int totalAdcValue = 0;

91 | P a g e

for (int i = 0; i < numReadings_Battery; i++) {

totalAdcValue += analogRead(Battery_adcPin) ;

// totalAdcValue += (analogRead(Battery_adcPin) * 0.9);

}

int adcValue = totalAdcValue / numReadings_Battery; //average

float measuredVoltage = (adcValue / (float)Battery_adcMaxValue) * referenceVoltage;

float batteryVoltage = measuredVoltage / Battery_voltageDividerRatio;

batteryVoltage = batteryVoltage / VoltageBattery_Calibration ;

Serial.print("ADC Value: ");

Serial.print(adcValue);

Serial.print(" | Measured Voltage: ");

Serial.print(measuredVoltage, 2);

Serial.print("V | Battery Voltage: ");

Serial.print(batteryVoltage, 2);

return batteryVoltage;

}

int batteryPercentage_NL() {

float batteryVoltage = batteryVoltage_1();

int batteryPercentage = 0;

92 | P a g e

if (batteryVoltage >= 4.2) batteryPercentage = 100.0;

else if (batteryVoltage >= 4.15) batteryPercentage = 95 + (batteryVoltage - 4.15) * 5 / 0.05;

else if (batteryVoltage >= 4.1) batteryPercentage = 90 + (batteryVoltage - 4.1) * 5 / 0.05;

else if (batteryVoltage >= 4.0) batteryPercentage = 80 + (batteryVoltage - 4.0) * 10 / 0.1;

else if (batteryVoltage >= 3.9) batteryPercentage = 60 + (batteryVoltage - 3.9) * 20 / 0.1;

else if (batteryVoltage >= 3.8) batteryPercentage = 40 + (batteryVoltage - 3.8) * 20 / 0.1;

else if (batteryVoltage >= 3.7) batteryPercentage = 20 + (batteryVoltage - 3.7) * 20 / 0.1;

else if (batteryVoltage >= 3.5) batteryPercentage = 10 + (batteryVoltage - 3.5) * 10 / 0.2;

else if (batteryVoltage >= 3.3) batteryPercentage = (batteryVoltage - 3.3) * 10 / 0.2;

else batteryPercentage = 0;

//to make the readings more stable

if ((abs(batteryLevel - batteryPercentage) <= 20))

batteryPercentage = batteryLevel;

Serial.print("V | Battery Percentage: ");

Serial.print(batteryPercentage, 1);
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

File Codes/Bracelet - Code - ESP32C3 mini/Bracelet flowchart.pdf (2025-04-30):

Initialize hardware
(OLED, MLX90614, MAX30102, ESP-NOW)

Yes

No IR >40000

Read Surface body
temperature

Read IR value from
MAX30102

Display no object
detected

Calculate core body
temperature | Read battery voltage

Convert the voltage into
percentage
(Linear method)

Read the average
heart rate

No

Skip? Yes
(to skip O2
readings)

Yes

No

O2 >= Minimum
accepted value? Read the O2 value

Save O2 value
Skip = True
Reset count of false
reading

count of false reading
++

Count of Iteration ++

Yes

No

Count of false
reading >= 20 ?

Skip = True
Reset count of false
reading

SPO2 Function

Count >= delay
iteration ?

Skip = False
count of iteration
= 0

Yes
This function starts by continuously reading the O₂ value until an acceptable value is received. Once that happens, the skip mode is activated. If a specific number of false O₂ readings (e.g., 20) is reached, the skip mode will be activated as well. When skip mode is active, the O₂ reading will be skipped for a specific number of iterations..

Reading the O₂ value causes significant delays in the code and affects other readings (especially heart rate). This function is designed to solve that problem.

Yes

No | 3 second has
| passed?

No

Display data
Send data Via ESP-Now

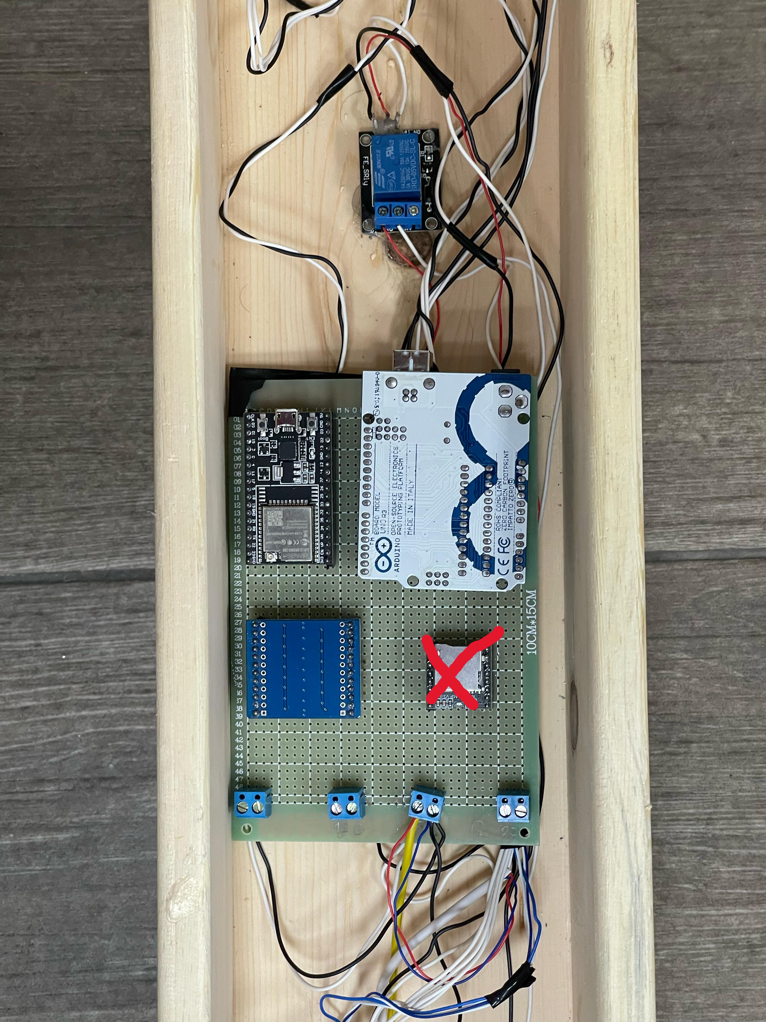
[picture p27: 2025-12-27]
Photo/circ.jpeg

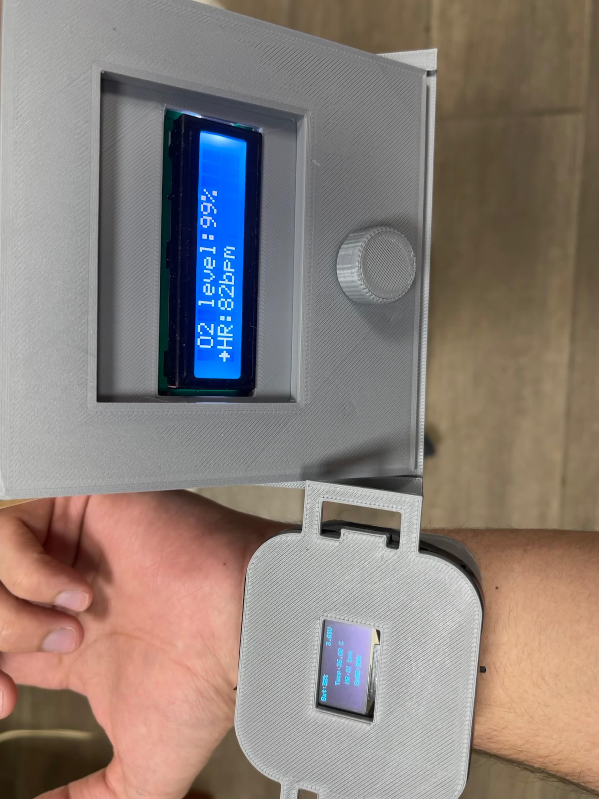
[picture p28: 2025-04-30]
Photo/WhatsApp Image 2025-04-23 at 17.41.56_e41d912d.jpg

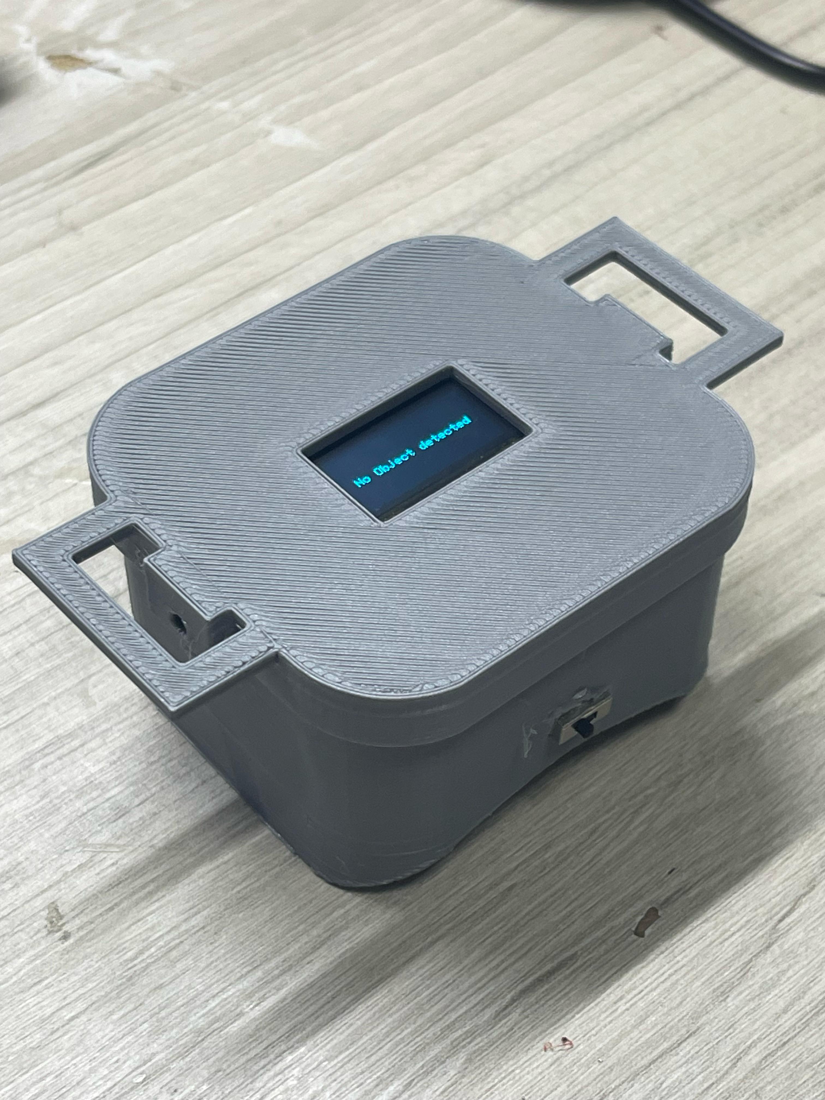
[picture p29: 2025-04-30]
Photo/no object.jpg

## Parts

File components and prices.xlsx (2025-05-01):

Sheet: Sheet2
Status | (All)
Store | (All)
Row Labels | Sum of total Price | Count of Quantity
0.5mm Copper Wire OK Line 30AWG | 5 | 1
0.5mm Copper Wire OK Line 30AWG | 5 | 1
0.96 inch IIC Serial (i2c) | 3 | 1
0.96" Inch Blue I2C IIC OLED LCD Module 4pin | 4 | 1
1 mm copper wired black color | 2 | 1
1 Push button - switch | 0.25 | 1
10*15 PCB Green Board Prototype | 7 | 1
1pcs - 3 Pin Switch | 0.75 | 2
2.54mm Single Row Female 1X40 Pin Header Strip Black | 0.99 | 1
3 in one wire (0.5mm each) | 1.4 | 1
3.2 inch 320 * 240 SPI Serial TFT LCD module | 30 | 2
392 Square Plastic Fuse | 0.4 | 1
40Pin 2.54mm Round male Pin Header | 0.3 | 1
40Pin 2.54mm Single Row Round Female Pin Header | 0.99 | 1
8 Channel Logic Level Converter Bi-Directional Module | 2 | 1
Bearing standard 22 mm | 0 | 1
Bearings 6008-2RS | 15 | 1
big pin (40 g) (1.5h) | 3 | 1
Black tape | 1 | 1
BTS7960 Motor Driver | 7 | 1
Circuit breaker
Connector | Straight Female Pin Header | 40x1 | 3x2.54mm | 1.2 | 1
CP-2515 Soldering Desoldering Wire Solder Wick | 3 | 1
Crib connector (750 g) (20h) | 48 | 1
Crib handles (40g)(1.5 h) |  | 1
E-Health Sensor | Oximeter | Heart-Rate | MAX30102 | 1.5 | 1
Encoder housing (40g) (2h) | 1.5 | 1
Encoder Module | Rotary | 0.9 | 1
ESP32-C3 Mini Development Board | 10 | 2
ESP32-CAM | 9 | 1
ESP32-WROOM-32U | 9 | 1
Fuse 25 A | 0.9 | 1
glue stick | 1 | 1
High Sensitivity Microphone Sensor Module | 3 | 1
KF300 2Pin Wire Terminal Copper | 1.2 | 1
Lithium Battery 502030 500mAh (3v - 4.2v) (chagrging 0.5c -1c) | 4.5 | 1
Lithium-polymer Battery | 3.7V 1500mAh | 50x40x6mm | 6 | 1
LM2596 DIP DC-DC Step Down Module | 3 | 1
Lower gear (100g 5.5H) | 3 | 1
Magnet | Bar 35x9x6mm | 1.5 | 1
Magnetic Sensor Encoder | Induction Angle Measurement Sensor | AS5600 | 1.5 | 1
MAX30102 Heart Rate and Pulse Oximeter Sensor Module | 2 | 1
Metal chassis | 70 | 1
Mini MP3 Player Module Board | 2 | 1
MLX90614 Non-Contact IR Temperature Sensor | 13 | 1
MLX90614 Non-Contact IR Temperature Sensor | 13 | 1
Motor Gear (140g) (4.5h) | 17.7 | 1
Motor Stand (140g) (6.5h) |  | 1
MT3608 2A Max DC-DC Step Up Power Module | 1.5 | 1
Relay
Resettable Fuse | RXE 160 | 2 | 1
Resistor 1.8k*2 - 1k - 4.7k - 1.2k*2 | 0.3 | 1
Resistor Carbon | 2W | 5% | 2K2 | 0.2 | 1
SD card 2gb | 2 | 1
SHT30-D Temperature Humidity Sensor | 3 | 1
Solder Wire 0.8mm 50g | 2 | 1
Speaker 8 Ohm 0.5W | 1.2 | 1
Speaker holder (100g) (3.5h) |  | 1
super glue | 0.5 | 1
Switching Power Supply 12V 30A | 12 | 1
Tactical Switch 4-Pin 6x6x4.3mm | 0.15 | 1
Thermoelectric Cooler Peltier 12705 12V 5A Cell | 11 | 1
three resistor (12k -30k -4.8k) | 0.15 | 1
Tinned Copper Jumper Wire 1m | 0.9 | 1
TP4056 Lithium Battery Charger Module | 2.5 | 1
USB 2.0 Mini Micro SD TF M2 Memory Card Reader | 1 | 1
USB type B mini | 2 | 1
Valio High torque Dc motor 12V | 20 | 1
Wiper motor 12v (new) | 30 | 1
Wires that can handle 20-30 A
wood and crib integration | 200 | 1
XL4015 5A DC to DC Step Down Module | 5 | 1
تنجيد | 80 | 1
(blank) | 30.47 | 3
Grand Total | 724.35 | 76

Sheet: Sheet1
Smart crib Components, prices, and links
Main components
Component | Quantity | total Price | Store | Links | Status | Additional information
ESP32-WROOM-32U | 1 | $9.00 | robot Pi Shop | ESP32-WROOM-32U – Robot Pi Shop (https://robotpishop.com/products/esp32-wroom-32u?_pos=9&_sid=659c80a50&_ss=r) | Available | e8:6b:ea:d4:7b:10c (MAC Adress) | Crib component | Electronics
ESP32-CAM | 1 | $9.00 | Electros | ESP32-CAM – Electroslab (https://electroslab.com/products/esp32-cam?_pos=5&_sid=c40614a91&_ss=r) | Available
SD card 2gb | 1 | $2.00 |  |  | Available
USB type B mini | 1 | $2.00 |  |  | Available
SHT30-D Temperature Humidity Sensor | 1 | $3.00 | Robot Pi Shop | SHT30-D Temperature Humidity Sensor – Robot Pi Shop (https://robotpishop.com/products/sht30-d-temperature-humidity-sensor?_pos=1&_sid=860517f7f&_ss=r) | Available | https://electropeak.com/learn/interfacing-sht30-temperature-humidity-sensor-with-arduino/
High Sensitivity Microphone Sensor Module | 1 | $3.00 | Electros | High Sensitivity Microphone Sensor Module – Electroslab (https://electroslab.com/products/high-sensitivity-microphone-sensor-module?_pos=1&_sid=4aa8680d6&_ss=r) | Available
Mini MP3 Player Module Board | 1 | $2.00 | Robot Pi Shop | Mini MP3 Player Module Board – Robot Pi Shop (https://robotpishop.com/products/mini-mp3-player-module-board?_pos=1&_sid=bb3df5edf&_ss=r) | Damaged | Wiring DFPlayer Mini (MP3 Module) to Arduino. Stereo/Mono Diagrams. - Circuit Journal
USB 2.0 Mini Micro SD TF M2 Memory Card Reader | 1 | $1.00 | Electros | USB 2.0 Mini Micro SD TF M2 Memory Card Reader – Electroslab (https://electroslab.com/products/usb-2-0-mini-micro-sd-tf-m2-memory-card-reader?_pos=1&_sid=bd4e653e9&_ss=r) | Available
Mini SD Card MP3 Sound Module | 1 | $4.00 | Electros | Mini SD Card MP3 Sound Module – Electroslab | Available | https://youtu.be/JJxWjqTkAyo?si=UZpOuHdPmap0ZqpK
Speaker 8 Ohm 0.5W | 2 | $1.20 | robot Pi Shop | Speaker 8 Ohm 0.5W – Robot Pi Shop (https://robotpishop.com/products/speaker-8-ohm-0-5w?_pos=3&_sid=190c99a99&_ss=r) | Available
Valio High torque Dc motor 12V | 1 | $20.00 |  |  | uncompatible
Wiper motor 12v (new) | 1 | $30.00 | Beb el ramel |  | Available
BTS7960 Motor Driver | 1 | $7.00 | robot Pi Shop | BTS7960 Motor Driver – Robot Pi Shop | Available | How to Use BTS7960 Motor Driver: Pinouts, Specs, and Examples | Cirkit Designer
Magnetic Sensor Encoder | Induction Angle Measurement Sensor | AS5600 | 1 | $1.50 | Katranji | https://rb.gy/txvuse | Available | AS5600 Magnetic Angle Encoder : 7 Steps (with Pictures) - Instructables
Magnet | Bar 35x9x6mm | 1 | $1.50 | Katranji | Magnet | Bar 35x9x6mm | Electronics Katrangi Trading | Available
Thermoelectric Cooler Peltier 12705 12V 5A Cell | 2 | $11.00 | Electros | Thermoelectric Cooler Peltier 12705 12V 5A Cell – Electroslab | Available
Relay |  |  |  |  | Available
Encoder Module | Rotary | 1 | $0.90 | Katranji | Encoder Module | Rotary | Electronics Katrangi Trading | Available | In-Depth: How Rotary Encoder Works and Interface It with Arduino
3.2 inch 320 * 240 SPI Serial TFT LCD module | 1 | $15.00 | Electros | 3.2 inch 320 * 240 SPI Serial TFT LCD module – Electroslab (https://electroslab.com/products/3-2-inch-320-240-spi-serial-tft-lcd-module?_pos=23&_sid=20e0b5813&_ss=r) | Available | Connecting an SPI TFT Touchscreen to Your Arduino – Bytes N Bits
3.2 inch 320 * 240 SPI Serial TFT LCD module | 1 | $15.00 | Electros | 3.2 inch 320 * 240 SPI Serial TFT LCD module – Electroslab (https://electroslab.com/products/3-2-inch-320-240-spi-serial-tft-lcd-module?_pos=23&_sid=20e0b5813&_ss=r) | Available
Switching Power Supply 12V 30A | 1 | $12.00 | robot Pi Shop | Switching Power Supply 12V 30A – Robot Pi Shop | Available
Circuit breaker |  |  |  |  | Available
Wires that can handle 20-30 A |  |  |  |  | Available
Fuse 25 A | 2 | $0.90 | Abou samra |  | Available
392 Square Plastic Fuse | 2 | $0.40 | Robot Pi Shop | 392 Square Plastic Fuse – Robot Pi Shop | Available
XL4015 5A DC to DC Step Down Module | 1 | $5.00 | robot Pi Shop | XL4015 5A DC to DC Step Down Module – Robot Pi Shop | Damaged
LM2596 DIP DC-DC Step Down Module | 1 | $3.00 | robot Pi Shop | LM2596 DIP DC-DC Step Down Module – Robot Pi Shop | Damaged
8 Channel Logic Level Converter Bi-Directional Module | 1 | $2.00 | robot Pi Shop | 8 Channel Logic Level Converter Bi-Directional Module – Robot Pi Shop | Available
PCB | 2 | $7.00 | robot Pi Shop | 10*15 PCB Green Board Prototype – Robot Pi Shop | Available
40Pin 2.54mm Round male Pin Header | 3 | $0.30 | robot Pi Shop | 40Pin 2.54mm Round male Pin Header – Robot Pi Shop | Available
2.54mm Single Row Female 1X40 Pin Header Strip Black | 3 | $0.99 | Electros | 2.54mm Single Row Female 1X40 Pin Header Strip Black – Electroslab | Available
40Pin 2.54mm Single Row Round Female Pin Header | 3 | $0.99 | Electros | 40Pin 2.54mm Single Row Round Female Pin Header – Electroslab | uncompatible
Connector | Straight Female Pin Header | 40x1 | 3x2.54mm | 2 | $1.20 | Katranji | Connector | Straight Female Pin Header | 40x1 | 3x2.54mm | Electronics Katrangi Trading | Available
KF300 2Pin Wire Terminal Copper | 4 | $1.20 | robot Pi Shop | KF300 2Pin Wire Terminal Copper – Robot Pi Shop | Available
Solder Wire 0.8mm 50g | 1 | $2.00 | Electros | Solder Wire 0.8mm 50g – Electroslab | Available
CP-2515 Soldering Desoldering Wire Solder Wick | 1 | $3.00 | robot Pi Shop | CP-2515 Soldering Desoldering Wire Solder Wick – Robot Pi Shop | Available
0.5mm Copper Wire OK Line 30AWG | 1 | $5.00 | robot Pi Shop | 0.5mm Copper Wire OK Line 30AWG 230m – Robot Pi Shop | uncompatible
0.5mm Copper Wire OK Line 30AWG | 230m | $5.00 | robot Pi Shop | 0.5mm Copper Wire OK Line 30AWG 230m – Robot Pi Shop | uncompatible
1 mm copper wired black color | 6 m | $2.00 | Abou samra |  | Available
0.5 mm copper wire black and white | 6m | $6.00
3 in one wire (0.5mm each) | 5 m | $1.40 | Abou samra |  | Available
Tinned Copper Jumper Wire 1m | 6 | $0.90 | robot Pi Shop | Tinned Copper Jumper Wire 1m – Robot Pi Shop | Available
ESP32-C3 Mini Development Board | 1 | $5.00 | Robot Pi Shop | https://shorturl.at/0oLWI | Damaged | ESP32 C3 Super Mini Development Board Details, Pinout, Specs | Bracelet component
ESP32-C3 Mini Development Board | 1 | $5.00 | Robot Pi Shop | https://shorturl.at/0oLWI | Available | ESP32 C3 Super Mini Development Board Details, Pinout, Specs
E-Health Sensor | Oximeter | Heart-Rate | MAX30102 | 1 | $1.50 | Katranji | E-Health Sensor | Oximeter | Heart-Rate | MAX30102 | Electronics Katrangi Trading | Available | https://rb.gy/a9w9qq
MAX30102 Heart Rate and Pulse Oximeter Sensor Module | 1 | $2.00 | Robot Pi Shop | https://shorturl.at/9POyD | Damaged | https://rb.gy/a9w9qq
MLX90614 Non-Contact IR Temperature Sensor | 1 | $13.00 | Electros | MLX90614 Non-Contact IR Temperature Sensor – Electroslab | Available
MLX90614 Non-Contact IR Temperature Sensor | 1 | $13.00 | Robot Pi Shop | MLX90614 Non-Contact IR Temperature Sensor – Robot Pi Shop (https://robotpishop.com/products/gy-906-mlx90614esf?variant=40764265693317) | Damaged
0.96" Inch Blue I2C IIC OLED LCD Module 4pin | 1 | $4.00 | Electros | 0.96" Inch Blue I2C IIC OLED LCD Module 4pin – Electroslab | Available
0.96 inch IIC Serial (i2c) | 1 | $3.00 | Robot Pi Shop | 0.96 inch IIC Serial – Robot Pi Shop (https://robotpishop.com/products/0-96-inch-iic-serial?variant=40764307406981) | Damaged | Soldered_333099-3395096.pdf (https://www.mouser.com/datasheet/2/1398/Soldered_333099-3395096.pdf)
Lithium-polymer Battery | 3.7V 1500mAh | 50x40x6mm | 1 | $6.00 | Katranji | Lithium-polymer Battery | 3.7V 1500mAh | 50x40x6mm | Electronics Katrangi Trading | Available
Lithium Battery 502030 500mAh (3v - 4.2v) (chagrging 0.5c -1c) | 1 | $4.50 | Robot Pi Shop | Lithium Battery 502030 – Robot Pi Shop (https://robotpishop.com/products/lithium-battery-502030?_pos=11&_sid=7f259e1e4&_ss=r) | uncompatible | LP502030.pdf (https://www.allboka.com/allboka/wp-content/boka/GuiGeYe/LiIonPloyDianChiGuiGeYe/LP502030.pdf)
TP4056 Lithium Battery Charger Module | 1 | $2.50 | Robot Pi Shop | TP4056 Lithium Battery Charger Module – Robot Pi Shop (https://robotpishop.com/products/tp4056-lithium-battery-charger-module?_pos=1&_sid=9c37979eb&_ss=r) | Available | 复件 tp4056_42_English_空页脚.doc (https://dlnmh9ip6v2uc.cloudfront.net/datasheets/Prototyping/TP4056.pdf?utm_source=chatgpt.com)
Resettable Fuse | RXE 160 1.6A | 2 | $2.00 | Katranji | Resettable Fuse | RXE 160 | Electronics Katrangi Trading | Available
Resistor Carbon | 2W | 5% | 2K2 | 2 | $0.20 | Katranji | Resistor Carbon | 2W | 5% | 2K2 | Electronics Katrangi Trading | Available
Resistor 1.8k*2 - 1k - 4.7k - 1.2k*2 | 6 | $0.30 | Robot Pi Shop | Resistor KOhms 1/4 Watt – Robot Pi Shop | Available
MT3608 2A Max DC-DC Step Up Power Module | 1 | $1.50 | Electros | MT3608 2A Max DC-DC Step Up Power Module – Electroslab (https://electroslab.com/products/mt3608-2a-max-dc-dc-step-up-power-module?_pos=3&_sid=0b3e98aa1&_ss=r) | Available | FEATURES (https://www.olimex.com/Products/Breadboarding/BB-PWR-3608/resources/MT3608.pdf)
three resistor (12k -30k -4.8k) | 3 | $0.15 | Robot Pi Shop | Resistor KOhms 1/4 Watt – Robot Pi Shop (https://robotpishop.com/products/resistor-kohms-1-4-watt?variant=40960628883589) | Available
1pcs - 3 Pin Switch | 2 | $0.50 | Electros | 1pcs - 3 Pin Switch – Electroslab (https://electroslab.com/products/3-pin-switch?_pos=3&_sid=a342e19f8&_ss=r) | Damaged
1pcs - 3 Pin Switch | 1 | $0.25 | Electros | 1pcs - 3 Pin Switch – Electroslab (https://electroslab.com/products/3-pin-switch?_pos=3&_sid=a342e19f8&_ss=r) | Damaged
1 Push button - switch | 1 | $0.25 | Robot Pi Shop | https://shorturl.at/4Vp90 | uncompatible
Tactical Switch 4-Pin 6x6x4.3mm | 1 | $0.15 | Robot Pi Shop | https://shorturl.at/4xg0f | uncompatible
Crib connector (750 g) (20h) | 2 | $48.00 |  |  | Available |  | 3d printed | Structure
big pin (40 g) (1.5h) | 3 | $3.00 |  |  | Available
Encoder housing (40g) (2h) | 1 | $1.50 |  |  | Available
Motor Gear (140g) (4.5h) | 1 | $17.70 |  |  | Available
Motor Stand (140g) (6.5h) | 1 |  |  |  | Available
Speaker holder (100g) (3.5h) | 1 |  |  |  | Available
Crib handles (40g)(1.5 h) | 2 |  |  |  | Available
Screen holder | 1 | $8.00 |  |  | Available
small parts | -
Lower gear (100g 5.5H) | 1 | $3.00 |  |  | Available |  | mechanical
Bearings 6008-2RS | 3 | $15.00 |  |  | Available
Bearing standard 22 mm | 1 | $0.00 |  |  | Available
Metal chassis | 1 | $70.00 |  |  | Available
wood and crib integration | 1 | $200.00 |  |  | Available
تنجيد | - | $80.00 |  |  | Available
 | VAT | $1.47 | Electonics | $263.18
 | Shipping | $37.00 | Structure | $446.20
 | $747.85

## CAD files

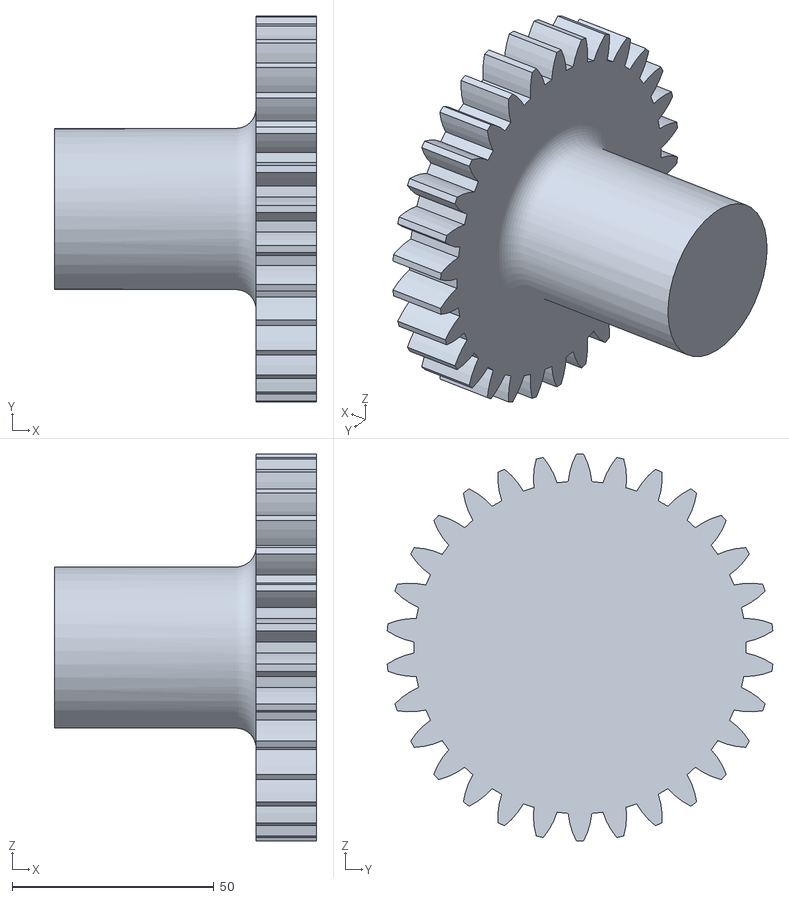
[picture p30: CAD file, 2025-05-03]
Drawing - Mechanical Parts/BE-STLs/gear test 3 (Part)-full shaft.STL
65.0 x 95.6 x 96.0

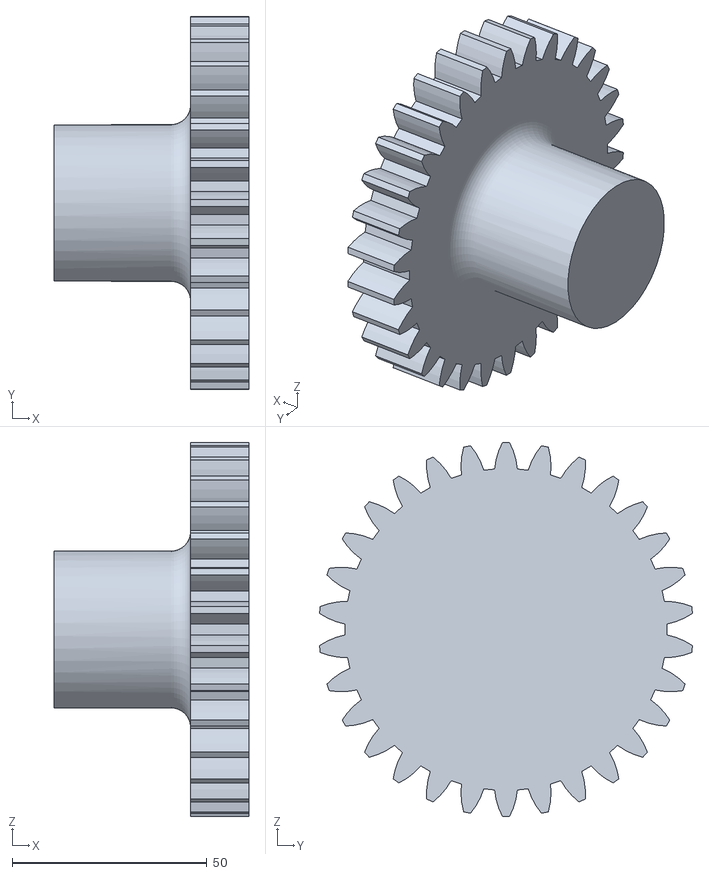
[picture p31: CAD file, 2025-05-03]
Drawing - Mechanical Parts/BE-STLs/gear test 3 (Part)-Motor-full shaft.STL
50.0 x 95.6 x 96.0

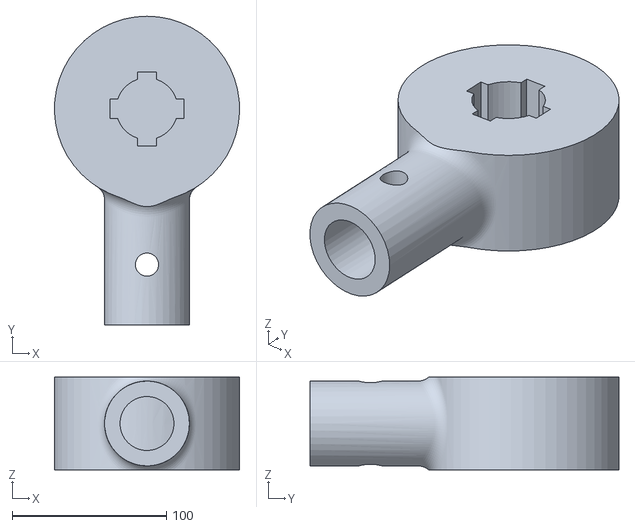
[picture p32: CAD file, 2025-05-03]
Drawing - Mechanical Parts/BE-STLs/crib connector/Crib-BallBearing-Connector-5-final-test.STL
119.9 x 200.0 x 60.0

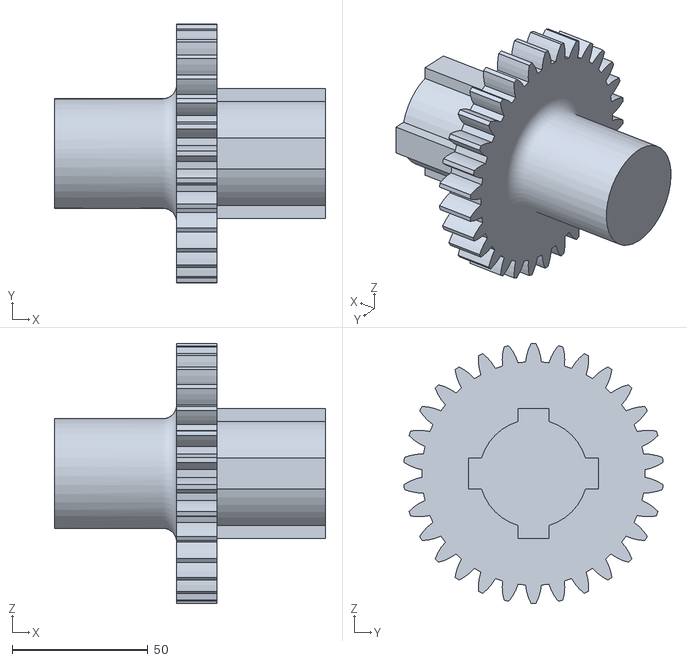
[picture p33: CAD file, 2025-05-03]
Drawing - Mechanical Parts/BE-STLs/gear test 3 lower.STL
100.0 x 95.6 x 96.0

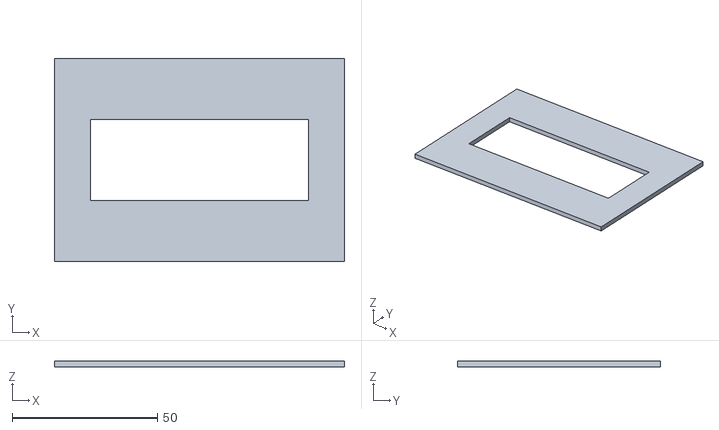
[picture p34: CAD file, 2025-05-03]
Drawing - Mechanical Parts/BE-STLs/screen changer.stl
100.0 x 70.0 x 2.00

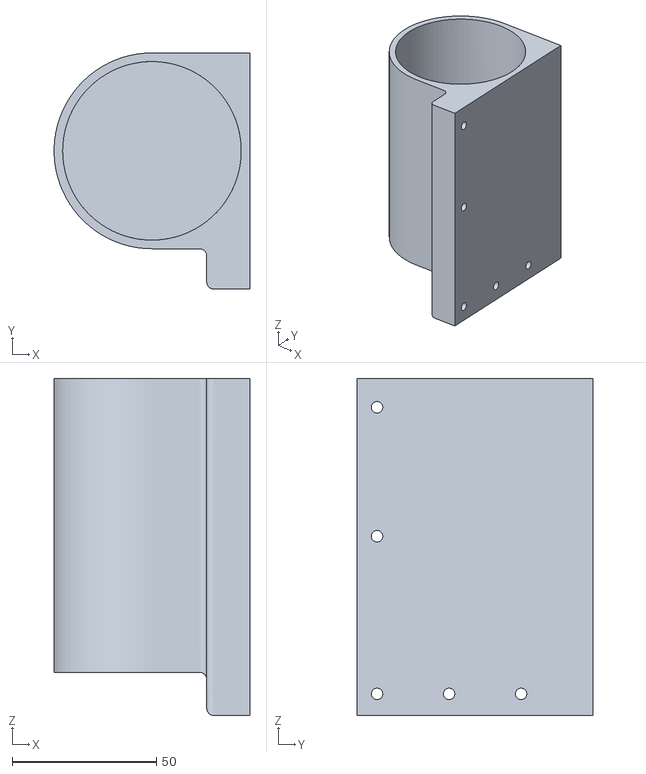
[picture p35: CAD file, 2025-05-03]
Drawing - Mechanical Parts/BE-STLs/Motor Holder v3.stl
68.0 x 82.0 x 117.0

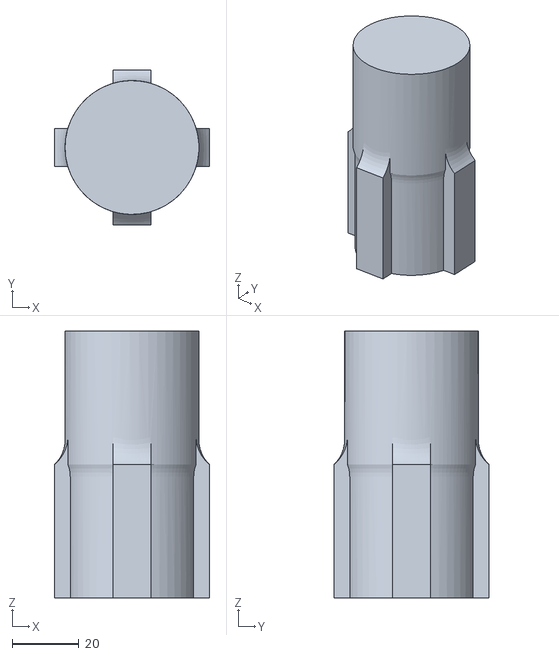
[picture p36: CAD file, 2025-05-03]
Drawing - Mechanical Parts/BE-STLs/big Pin4.STL
46.5 x 46.5 x 80.0

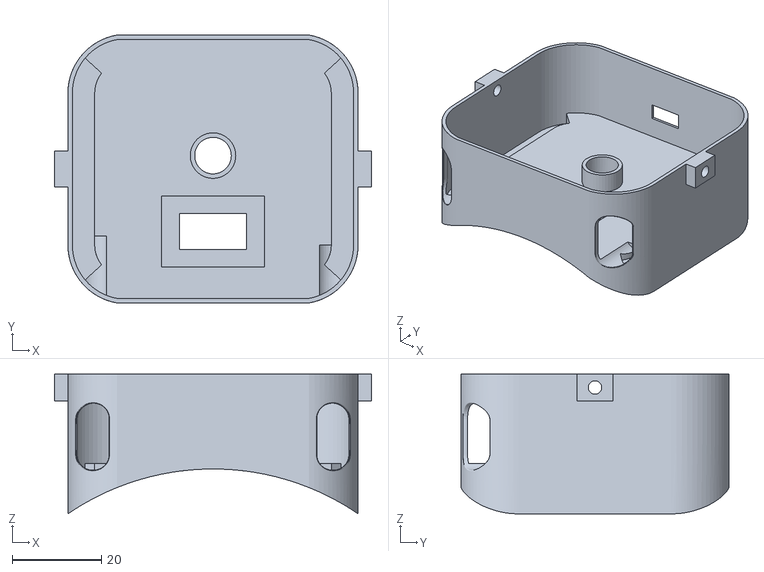
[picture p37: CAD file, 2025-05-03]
Drawing - Mechanical Parts/BE-STLs/Baby Monitor 2v2 v6.stl
71.0 x 60.0 x 31.3

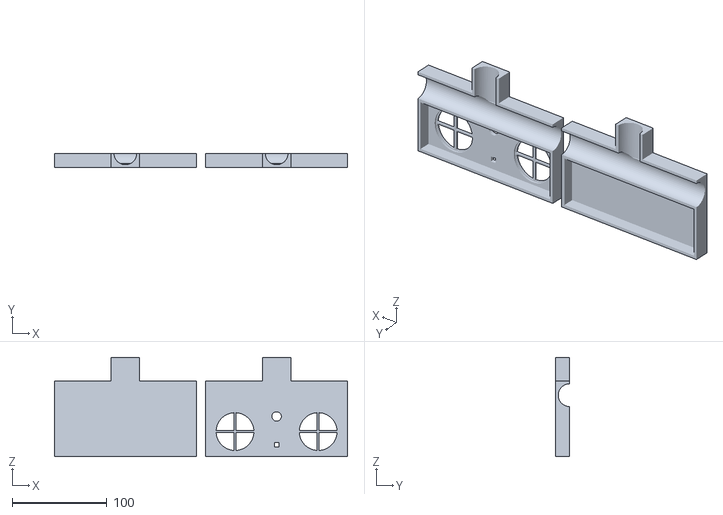
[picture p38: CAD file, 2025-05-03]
Drawing - Mechanical Parts/BE-STLs/speaker-temp chanber v0.stl
310.0 x 15.0 x 105.0

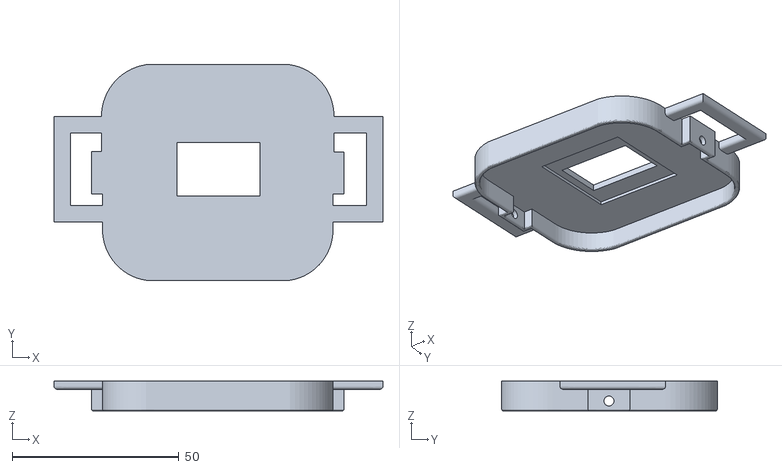
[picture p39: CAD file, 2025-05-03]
Drawing - Mechanical Parts/BE-STLs/cover 2 v3.stl
98.8 x 64.7 x 9.00

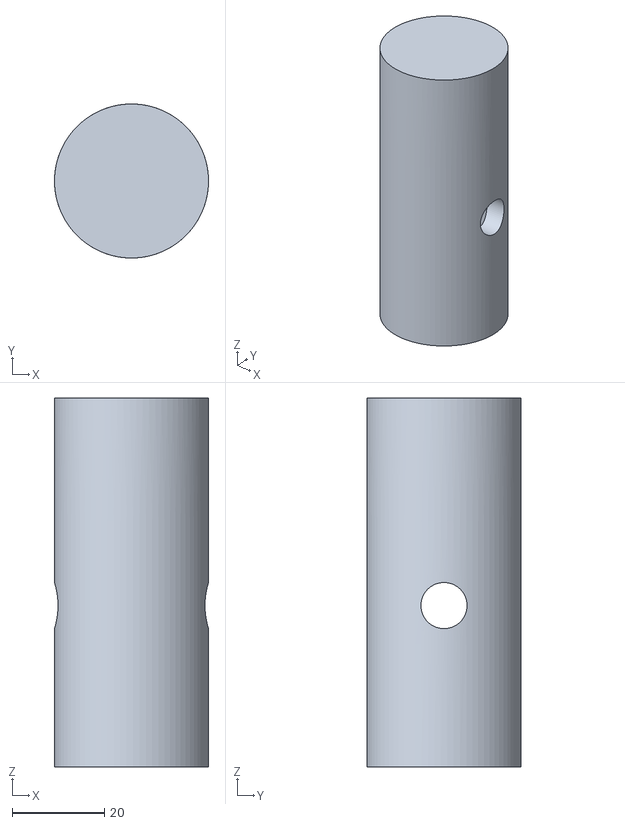
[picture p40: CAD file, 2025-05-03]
Drawing - Mechanical Parts/BE-STLs/calibrator v3.stl
33.4 x 33.4 x 80.0

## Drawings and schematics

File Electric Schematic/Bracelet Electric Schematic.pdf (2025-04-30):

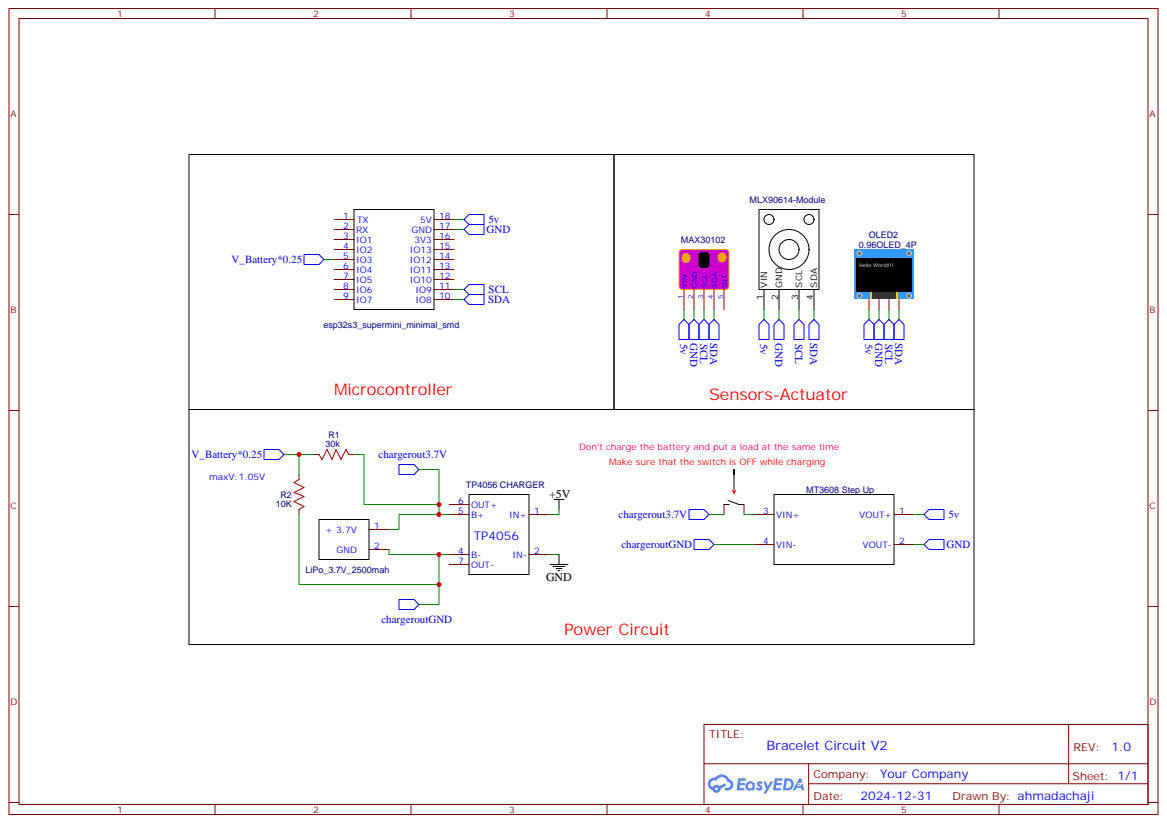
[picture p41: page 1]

Don't charge the battery and put a load at the same time
Make sure that the switch is OFF while charging

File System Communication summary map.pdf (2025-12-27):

## 1-ESP32C3 mini

Communication protocol | Sybmbol

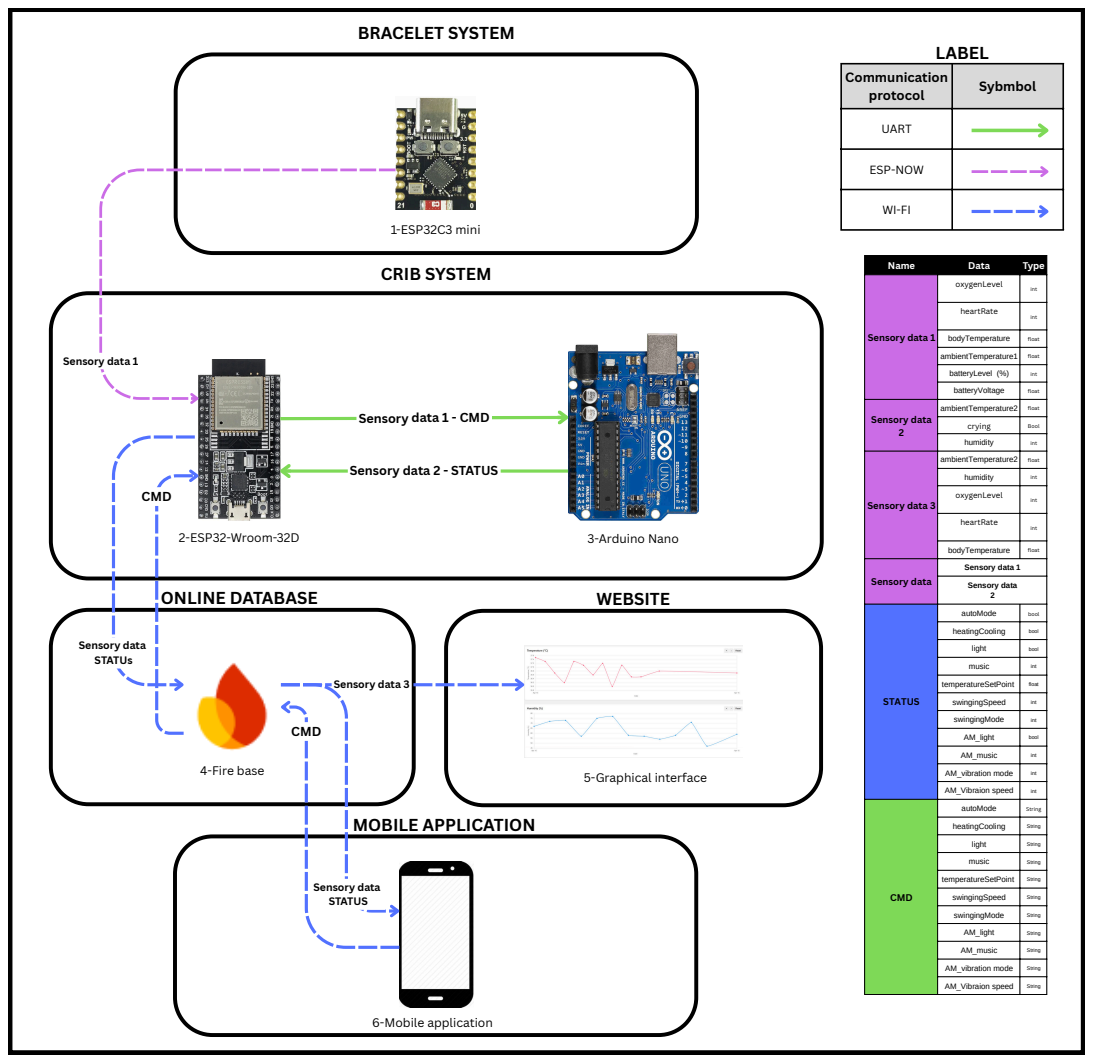
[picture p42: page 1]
CRIB SYSTEM; Sensory data 1; 2-ESP32-Wroom-32D; CMD; 4-Fire base; MOBILE APPLICATION; Sensory data 3; 3-Arduino Nano; BRACELET SYSTEM; ONLINE DATABASE; WEBSITE; LABEL; 5-Graphical interface; 6-Mobile application; Sensory data 2

UART

ESP-NOW

Name | Data | Type
Sensory data 1 | oxygenLevel | int

heartRate | int

bodyTemperature | float

ambientTemperature1 | float

batteryLevel (%) | int

batteryVoltage | float

Sensory data 2 | ambientTemperature2 | float

Sensory data 1 - CMD

crying | Bool
humidity | int

Sensory data 2 - STATUS

Sensory data 3 | ambientTemperature2 | float

oxygenLevel | int

Sensory data | Sensory data 1

STATUS | autoMode | bool

heatingCooling | bool

Sensory data STATUs

light | bool

music | int

temperatureSetPoint | float

swingingSpeed | int

swingingMode | int

AM_light | bool

AM_music | int

AM_vibration mode | int

AM_Vibraion speed | int

CMD | autoMode | String

heatingCooling | String

light | String

music | String

Sensory data STATUS

temperatureSetPoint | String

swingingSpeed | String

swingingMode | String

AM_light | String

AM_music | String

AM_vibration mode | String

AM_Vibraion speed | String

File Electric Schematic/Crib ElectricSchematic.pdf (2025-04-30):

# D0 11 D1 12 D2 13 D3 14 D4 15 D5 16 D6 17 D7 18

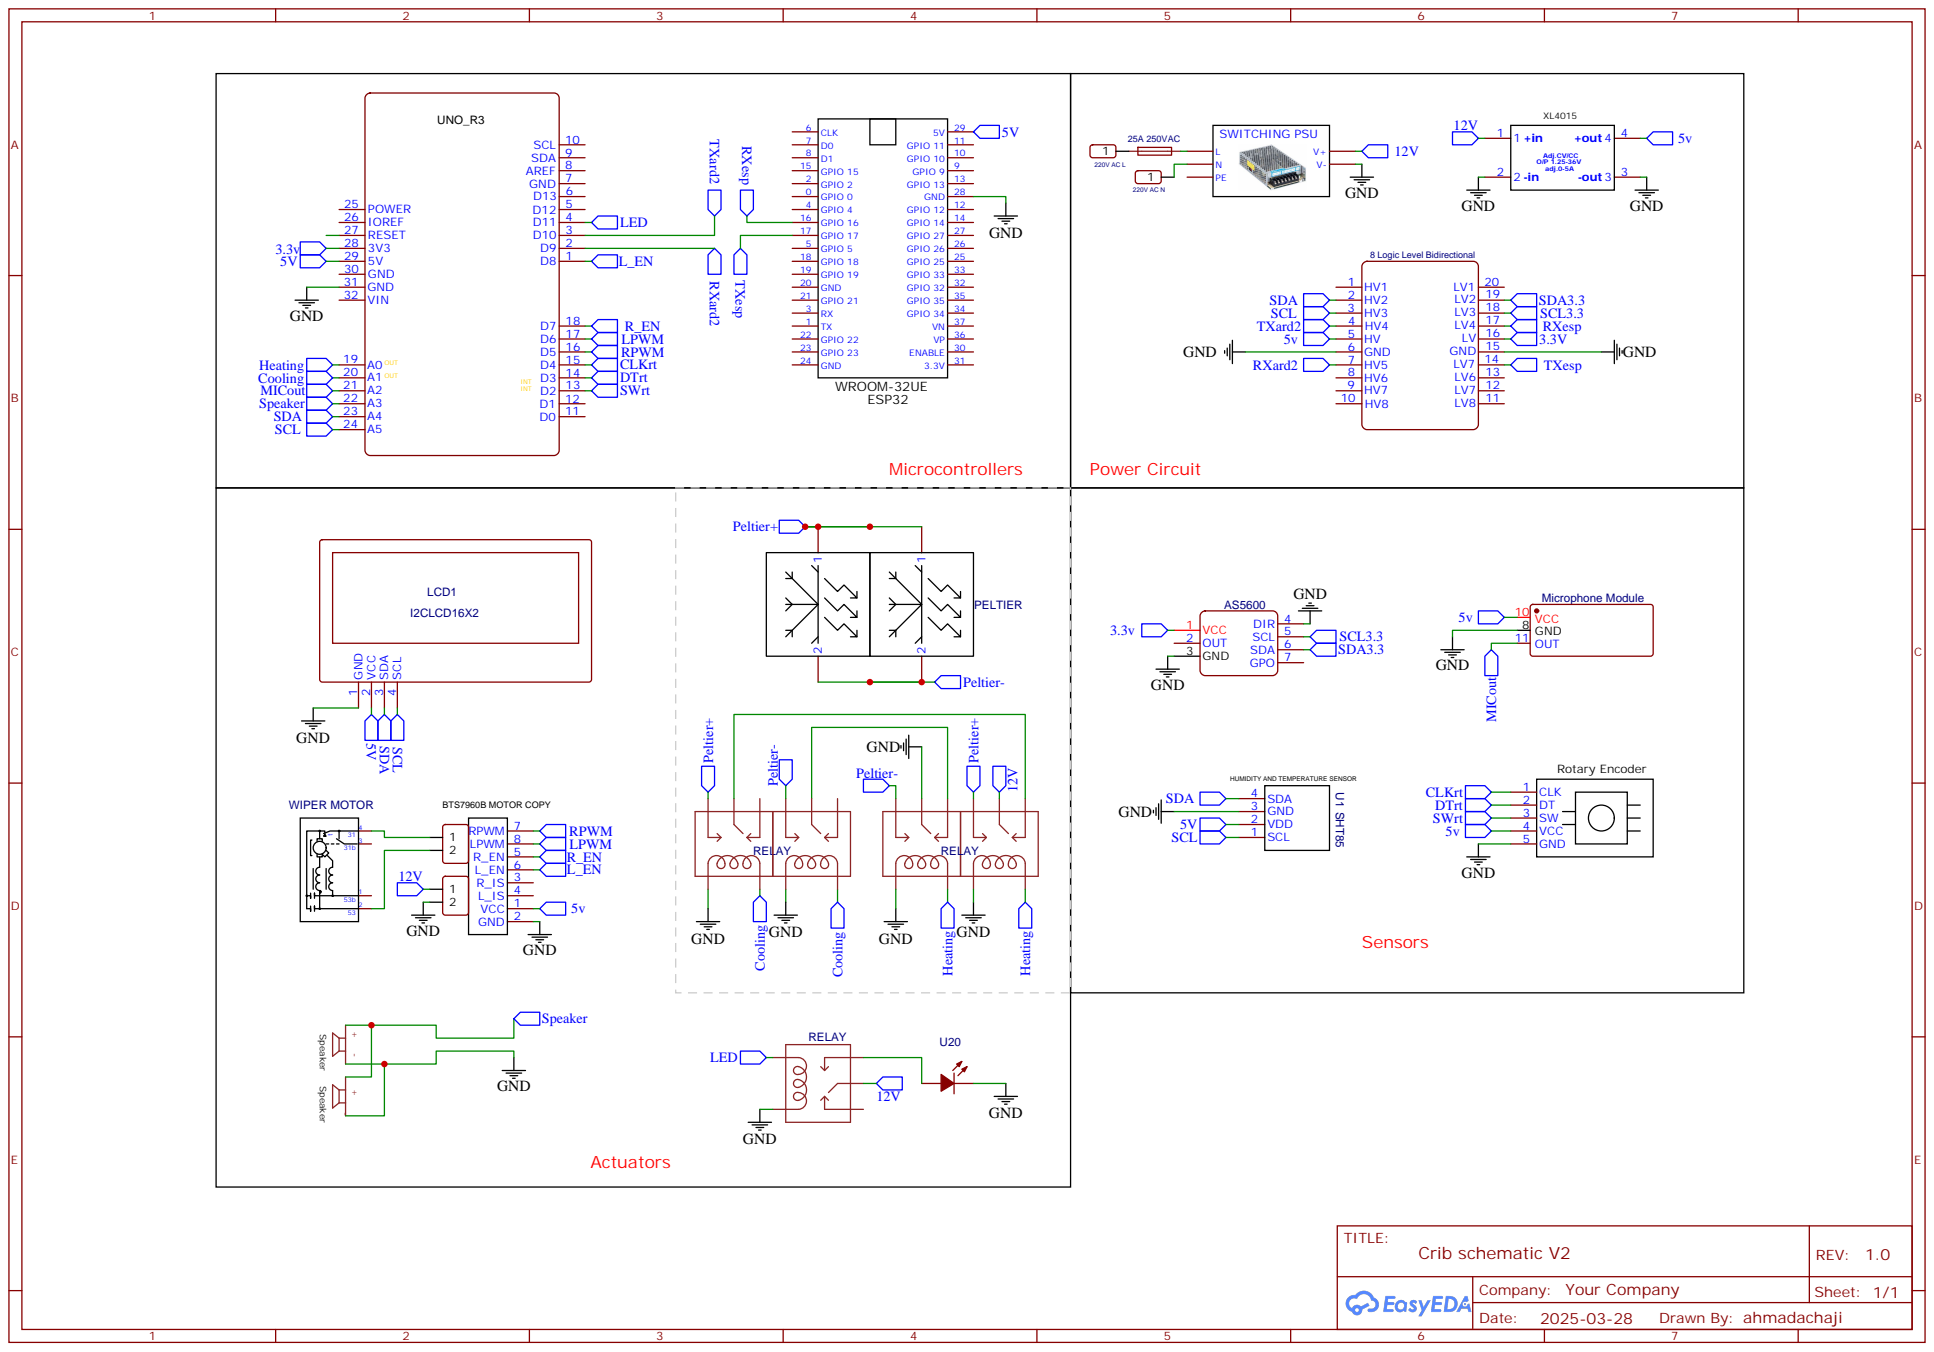
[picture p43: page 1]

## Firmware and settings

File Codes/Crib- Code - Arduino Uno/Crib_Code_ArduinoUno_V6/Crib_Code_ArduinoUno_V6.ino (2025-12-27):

#include <Wire.h>
#include <LiquidCrystal_I2C.h>
#include <SoftwareSerial.h>


// ====== MOTOR + ENCODER CONFIG ======
#define RPWM 5
#define LPWM 6
#define R_EN 7
#define L_EN 8
#define MOTOR_SPEED 25
#define MIC_PIN A2
#define CLK 4
#define DT 3
#define SW 2
#define RELAY_LIGHT 11

#define ESP_RX 9
#define ESP_TX 10

LiquidCrystal_I2C lcd(0x27, 16, 2);
SoftwareSerial espSerial(ESP_RX, ESP_TX);

uint8_t arrow[8] = { 0x00, 0x04, 0x06, 0x1F, 0x06, 0x04, 0x00 };

const char* menuItems[] = {
  "O2 level", "HR", "Body T", "Ambient T",
  "Humidity: 70%", "Battery", "Crying", "Motor",
  "Music", "Light", "Cooling/Heating", "Auto Mode"
};
const int menuLength = sizeof(menuItems) / sizeof(menuItems[0]);

enum ScreenState { MENU,
                   MOTOR_OPTIONS,
                   LIGHT_OPTIONS,
                   MUSIC_OPTIONS,
                   AUTO_MODE_OPTIONS };
ScreenState currentScreen = MENU;

int soundThreshold = 5;
int cryingMinDuration = 50;
int counter = 0;
int lastClkState;
bool swPressed = false;
unsigned long swPressedTime = 0;
unsigned long lastSensorUpdate = 0;
unsigned long lastCryCheck = 0;
const unsigned long cryCheckInterval = 25000;  // 10 seconds
bool babyCryDetected = false;
const unsigned long sensorTimeout = 3000;  // 3 seconds
bool swHandled = false;
bool detectBabyCry(int soundThreshold = 16, int cryingMinDuration = 42);
bool motorRunning = false;
bool returningToHome = false;
int motorToggle = 0;
float initialAngle = 0;
bool swingRight = true;
int lightToggle = 0;
int musicSelection = 0;
bool autoModeOn = false;
int autoModeToggle = 0;

// ====== SENSOR DATA STRUCT ======
typedef struct __attribute__((packed)) {
  uint16_t bodyTemp;
  uint16_t ambientTemp;
  uint8_t heartRate;
  uint8_t oxygenLevel;
  uint8_t batteryLevel;
  uint8_t batteryVolt;
} SensorData;

SensorData incomingData;
bool newSensorData = false;

// ====== AS5600 SENSOR ======
class AS5600Sensor {
public:
  const uint8_t address = 0x36;

  bool begin() {
    Wire.begin();
    Wire.setClock(400000L);
    return checkMagnet();
  }

  bool checkMagnet() {
    Wire.beginTransmission(address);
    Wire.write(0x0B);
    Wire.endTransmission();
    Wire.requestFrom((uint8_t)address, (uint8_t)1);
    if (Wire.available()) {
      byte status = Wire.read();
      return status & 0x20;
    }
    return false;
  }

  float readAngle() {
    Wire.beginTransmission(address);
    Wire.write(0x0C);
    Wire.endTransmission();
    Wire.requestFrom((uint8_t)address, (uint8_t)2);
    if (Wire.available() >= 2) {
      byte highByte = Wire.read();
      byte lowByte = Wire.read();
      int raw = ((highByte & 0x0F) << 8) | lowByte;
      return raw * (360.0 / 4096.0);
    }
    return -1;
  }
};

AS5600Sensor encoder;

// === SONG DATA ===
const int speakerPin = A3;


const int melody1[] PROGMEM = {
  262,262,392,392,440,440,392,349,349,330,330,294,294,262,
  392,392,349,349,330,330,294,392,392,349,349,330,330,294,
  262,262,392,392,440,440,392,349,349,330,330,294,294,262,
  294,294,262,262,294,294,330,330,349,330,294,262,294,330,
  392,392,349,330,294,262,262
};
const int duration1[] PROGMEM = {
  500,500,500,500,500,500,1000,500,500,500,500,500,500,1000,
  500,500,500,500,500,500,1000,500,500,500,500,500,500,1000,
  500,500,500,500,500,500,1000,500,500,500,500,500,500,1000,
  500,500,500,500,500,500,700,500,500,500,500,500,500,1000,
  500,500,500,500,500,800,1000
};
const int melody2[] PROGMEM = {
  330,294,262,294,330,330,330,294,294,294,330,392,392,
  330,330,330,294,262,262,294,294,330,330,330,294,330,
  330,294,262,262,330,330,330,294,294,294,330,392,392,
  330,330,330,294,262,262
};
const int duration2[] PROGMEM = {
  400,400,400,400,400,400,800,400,400,800,400,400,800,
  400,400,400,400,400,400,800,400,400,400,400,400,400,
  800,400,400,400,400,400,400,800,400,400,400,400,400,
  400,800,400,400,400,400,400,400
};
const int melody3[] PROGMEM = {
  264,264,297,264,352,330,264,264,297,264,396,352,
  264,264,297,264,352,330,264,264,297,264,396,352,
  264,264,297,264,352,330,264,264,297,264,396,352,
  264,264,297,264,352,330
};
const int duration3[] PROGMEM = {
  350,350,700,700,700,1400,350,350,700,700,700,1400,
  350,350,700,700,700,1400,350,350,700,700,700,1400,
  350,350,700,700,700,1400,350,350,700,700,700,1400,
  350,350,700,700,700,1400
};

const int NUM_SONGS = 3;
int* melodies[NUM_SONGS] = { melody1, melody2, melody3 };
int* durations[NUM_SONGS] = { duration1, duration2, duration3 };
int melodyLengths[NUM_SONGS] = {
  sizeof(melody1) / sizeof(int),
  sizeof(melody2) / sizeof(int),
  sizeof(melody3) / sizeof(int)
};

int* currentMelody = nullptr;
int* currentDurations = nullptr;
int currentSongLength = 0;
int currentNote = 0;
bool isTonePlaying = false;
bool isPlaying = false;
unsigned long previousMillis = 0;
unsigned long autoModeStartTime = 0;
bool autoModeActive = false;

bool Automode_light_value=1; 
bool Automode_swinging_value=0; 
int Automode_music_value=0; 

void setup() {
  pinMode(CLK, INPUT_PULLUP);
  pinMode(DT, INPUT_PULLUP);
  pinMode(SW, INPUT_PULLUP);
  pinMode(RPWM, OUTPUT);
  pinMode(LPWM, OUTPUT);
  pinMode(R_EN, OUTPUT);
  pinMode(L_EN, OUTPUT);
  pinMode(RELAY_LIGHT, OUTPUT);
  pinMode(speakerPin, OUTPUT);

  digitalWrite(R_EN, HIGH);
  digitalWrite(L_EN, HIGH);
  

  lcd.init();
  lcd.backlight();
  lcd.createChar(0, arrow);

  Serial.begin(9600);
  espSerial.begin(9600);

  if (!encoder.begin()) {
    lcd.clear();
    lcd.setCursor(0, 0);
    lcd.print("Encoder Error!");
    while (1)
      ;
  }

  lastClkState = digitalRead(CLK);
  updateMenuDisplay();
}

void loop() {

  handleEncoderRotation();
  handleButtonPress();
  if (motorRunning) handleMotorSwing();
  if (returningToHome) returnToInitialAngle();
  if (isPlaying) updatePlayback();
  Recieving_Braceletsensors_CMD_data();
  if (millis() - lastCryCheck >= cryCheckInterval) {babyCryDetected = detectBabyCry(); lastCryCheck = millis(); updateMenuDisplay();}
  if (autoModeOn) hnadleAutoMode() ;

}
bool detectBabyCry(int soundThreshold, int cryingMinDuration) {
  static unsigned long soundStart = 0;
  static bool isLoud = false;

  int micValue = analogRead(MIC_PIN);
  if (micValue > soundThreshold) {
    if (!isLoud) {
      isLoud = true;
      soundStart = millis();
    }
  } else {
    if (isLoud) {
      unsigned long duration = millis() - soundStart;
      isLoud = false;
      if (duration >= cryingMinDuration) {
        Serial.println("🍼 Baby cry detected!");
        return true;
      }
    }
  }
  return false;
}


void playSong(int songNumber) {
  if (songNumber >= 0 && songNumber < NUM_SONGS) {
    currentMelody = melodies[songNumber];
    currentDurations = durations[songNumber];
    currentSongLength = melodyLengths[songNumber];
    currentNote = 0;
    isTonePlaying = false;
    isPlaying = true;

    switch (songNumber){
      case 0:sendStatusToESP("music_status", "1");break;
      case 1:sendStatusToESP("music_status", "2");break;
      case 2: sendStatusToESP("music_status", "3");break;
    }

    int songReal = songNumber+1; 
    Serial.print("Turning ON the music ");Serial.println(songReal);


  }
}
  void updatePlayback() {
    unsigned long currentMillis = millis();

    if (!isTonePlaying && currentNote < currentSongLength) {
      // Read note and duration from PROGMEM
      int note = pgm_read_word_near(currentMelody + currentNote);
      unsigned long dur = pgm_read_word_near(currentDurations + currentNote);

      tone(speakerPin, note);
      previousMillis = currentMillis;
      isTonePlaying = true;
    }

    if (isTonePlaying) {
      // Read duration from PROGMEM
      unsigned long dur = pgm_read_word_near(currentDurations + currentNote);

      if (currentMillis - previousMillis >= dur) {
        noTone(speakerPin);
        currentNote++;
        isTonePlaying = false;

        if (currentNote >= currentSongLength) {
          currentNote = 0;  // Restart the song instead of stopping
        }
      }
    }
  }
  void stopPlayback() {

    sendStatusToESP("music_status", "0");
    
    Serial.println("Music stoped");
    noTone(speakerPin);
    isPlaying = false;
  }


void handleEncoderRotation() {
  int currentClkState = digitalRead(CLK);
  if (currentClkState != lastClkState) {
    lastClkState = currentClkState;

    if (digitalRead(DT) != currentClkState) {
      if (currentScreen == MENU && counter < menuLength - 1) counter++;
      else if (currentScreen == MUSIC_OPTIONS && musicSelection < 3) musicSelection++;
    } else {
      if (currentScreen == MENU && counter > 0) counter--;
      else if (currentScreen == MUSIC_OPTIONS && musicSelection > 0) musicSelection--;
    }

    if (currentScreen == MENU) updateMenuDisplay();
    else if (currentScreen == MUSIC_OPTIONS) updateMusicSelectionDisplay();
  }
}


void handleButtonPress() {
  if (digitalRead(SW) == LOW) {
    if (!swPressed) {
      swPressed = true;
      swPressedTime = millis();
      swHandled = false;
    } else if (!swHandled && (millis() - swPressedTime > 1200)) {
      swHandled = true;
      currentScreen = MENU;
      updateMenuDisplay();
    }
  } else if (swPressed) {
    swPressed = false;
    if (!swHandled) {
      swHandled = true;

      if (currentScreen == MENU) {
        if (strcmp(menuItems[counter], "Motor") == 0) {
          currentScreen = MOTOR_OPTIONS;
          updateMotorOptionDisplay();
        } else if (strcmp(menuItems[counter], "Auto Mode") == 0) {
          currentScreen = AUTO_MODE_OPTIONS;
          updateAutoModeDisplay();
        } else if (strcmp(menuItems[counter], "Light") == 0) {
          currentScreen = LIGHT_OPTIONS;
          updateLightOptionDisplay();
        } else if (strcmp(menuItems[counter], "Music") == 0) {
          currentScreen = MUSIC_OPTIONS;
          musicSelection = 0;
          updateMusicSelectionDisplay();
        }
      } else if (currentScreen == MOTOR_OPTIONS) {
        
        startStopMotor(motorToggle == 0);

        if (motorRunning) {
          sendStatusToESP("swinging_status", "true");
          initialAngle = encoder.readAngle();
          swingRight = true;
          returningToHome = false;
        } else {
          
          returningToHome = true;
        }

        currentScreen = MENU;
        counter = 7;
        updateMenuDisplay();
      } else if (currentScreen == LIGHT_OPTIONS) {

        startStopLight ((lightToggle == 0) ? 1 : 0);

        currentScreen = MENU;
        counter = 9;
        updateMenuDisplay();
      } else if (currentScreen == MUSIC_OPTIONS) {
        if (musicSelection < NUM_SONGS) {
          playSong(musicSelection);
        } else {
          stopPlayback();
        }
        currentScreen = MENU;
        counter = 8;
        updateMenuDisplay();
      } else if (currentScreen == AUTO_MODE_OPTIONS) {

        startStopAutoMode(autoModeToggle == 0);

        if (!autoModeOn) returningToHome = true;

          //        currentScreen = MENU;
          //       counter = 11;
            //      updateMenuDisplay();
      }
    }
  }
}


void updateAutoModeDisplay() {
  lcd.clear();
  lcd.setCursor(0, 0);
  lcd.print("Auto Mode:");
  lcd.setCursor(1, 1);
  lcd.print(autoModeToggle == 0 ? "Turn ON" : "Turn OFF");
}
void updateMenuDisplay() {
  lcd.clear();
  int pageIndex = counter / 2;
  int startIndex = pageIndex * 2;

  for (int i = 0; i < 2; i++) {
    int itemIndex = startIndex + i;
    if (itemIndex >= menuLength) break;

    lcd.setCursor(0, i);
    lcd.print(" ");
    if (itemIndex == counter) lcd.setCursor(0, i), lcd.write(byte(0));
    lcd.setCursor(1, i);
    lcd.print(menuItems[itemIndex]);

    if (itemIndex != 7 && itemIndex != 8 && itemIndex != 9 && itemIndex != 10 && itemIndex != 11) {
      lcd.print(":");
    }
    if (itemIndex == 6) {
      lcd.print(":");
      lcd.print(babyCryDetected ? "yes" : "no");
    } else if (itemIndex == 11) {
      lcd.print(":");
      lcd.print(autoModeOn ? "ON" : "OFF");
    }


    if (newSensorData) {
      switch (itemIndex) {
        case 0:
          if (incomingData.oxygenLevel > 0) {
            lcd.print(incomingData.oxygenLevel);
            lcd.print("%");
          }
          break;
        case 1:
          if (incomingData.heartRate > 0) {
            lcd.print(incomingData.heartRate);
            lcd.print("bpm");
          }
          break;
        case 2:
          if (incomingData.bodyTemp > 0) {
            lcd.print(incomingData.bodyTemp / 100.0, 1);
            lcd.print("C");
          }
          break;
        case 3:
          if (incomingData.ambientTemp > 0) {
            lcd.print(incomingData.ambientTemp / 100.0, 1);
            lcd.print("C");
          }
          break;
        case 5:
          if (incomingData.batteryLevel > 0) {
            lcd.print(incomingData.batteryLevel);
            lcd.print("%");
          }
          break;
      }
    }
  }
}
void updateMotorOptionDisplay() {
  lcd.clear();
  lcd.setCursor(0, 0);
  lcd.print("Press to:");
  lcd.setCursor(1, 1);
  lcd.print(motorToggle == 0 ? "Turn ON" : "Turn OFF");
}
void updateLightOptionDisplay() {
  lcd.clear();
  lcd.setCursor(0, 0);
  lcd.print("Press to:");
  lcd.setCursor(1, 1);
  lcd.print(lightToggle == 0 ? "Turn ON" : "Turn OFF");
}
void updateMusicSelectionDisplay() {
  lcd.clear();
  lcd.setCursor(0, 0);
  lcd.print("Select Track:");
  lcd.setCursor(0, 1);
  lcd.write(byte(0));

  if (musicSelection < NUM_SONGS) {
    lcd.print(" Track ");
    lcd.print(musicSelection + 1);
  } else {
    lcd.print(" Stop Song");
  }
}


void handleMotorSwing() {
  float angle = encoder.readAngle();
  float targetAngle = swingRight ? initialAngle + 3 : initialAngle - 3;

  if (targetAngle > 360) targetAngle -= 360;
  if (targetAngle < 0) targetAngle += 360;

  float diff = angleDiff(angle, targetAngle);

  if (abs(diff) < 1.0) {
    swingRight = !swingRight;
    restMotor();
    delay(200);
  } else {
    if (diff > 0) {
      analogWrite(RPWM, MOTOR_SPEED);
      analogWrite(LPWM, 0);
    } else {
      analogWrite(RPWM, 0);
      analogWrite(LPWM, MOTOR_SPEED);
    }
  }
}
void returnToInitialAngle() {
  float currentAngle = encoder.readAngle();
  float error = angleDiff(currentAngle, initialAngle);

  if (abs(error) < 1.0) {
    restMotor();
    returningToHome = false;
  } else {
    if (error > 0) {
      analogWrite(RPWM, MOTOR_SPEED);
      analogWrite(LPWM, 0);
    } else {
      analogWrite(RPWM, 0);
      analogWrite(LPWM, MOTOR_SPEED);
    }
  }
}
float angleDiff(float from, float to) {
  float diff = fmod((to - from + 540), 360) - 180;
  return diff;
}
void restMotor() {
  analogWrite(RPWM, 0);
  analogWrite(LPWM, 0);
}


void hnadleAutoMode () {
    // If a cry is detected and Auto Mode isn't already running
    if (babyCryDetected && !autoModeActive) {
      autoModeStartTime = millis();
      autoModeActive = true;

      startStopMotor(Automode_swinging_value);
      startStopLight (Automode_light_value);

      if (Automode_music_value == -1)stopPlayback();
      else playSong(Automode_music_value);

      initialAngle = encoder.readAngle();
      swingRight = true;
      returningToHome = false;

    }

    // Stop after exactly 1 minute
    if (autoModeActive && millis() - autoModeStartTime >= 60000) {

      startStopAutoMode(0);
      returningToHome = true;  // Go back to initial angle
    }
}


void startStopMotor (bool on_off){
  if (on_off){
  motorRunning = 1 ; 
  motorToggle =1 ; 
  sendStatusToESP("swinging_status", "true");
  Serial.println("Swinging is set on.");
  }

  else {
    motorRunning =0;
    motorToggle = 0 ; 
    sendStatusToESP("swinging_status", "false");
    Serial.println("Swinging is set off.");
    analogWrite(RPWM, 0);
    analogWrite(LPWM, 0);
  }

}
void startStopLight (bool on_off){
  if (on_off == 1){
      digitalWrite(RELAY_LIGHT, HIGH);
      lightToggle = 1 ;
      sendStatusToESP("light_status", "true");
      Serial.println("Turning ON the light");
  }
  else {
    digitalWrite(RELAY_LIGHT, LOW);
    lightToggle = 0;
    sendStatusToESP("light_status", "false");
    Serial.println("Turning OFF the light");
  }
}
void startStopAutoMode (bool on_off){
  if (on_off){
    autoModeOn=true;
    autoModeToggle =1; 
    sendStatusToESP("automode_status", "true");
    Serial.println("Automode is set On");
  }
  else {
    autoModeOn=false;
    autoModeToggle = 0 ; 
    sendStatusToESP("automode_status", "false");
    Serial.println("Automode is set Off");

      stopPlayback();
      startStopMotor(0);
      startStopLight (0);
      autoModeActive = false; // stop runing 
  }

        currentScreen = MENU;
        counter = 11;
        updateMenuDisplay();
}


void Recieving_Braceletsensors_CMD_data() {
  if (!espSerial.available()) return;

  uint8_t startByte = espSerial.read();
  if (startByte != 0xAA) return;  // Wait for start byte

  unsigned long start = millis();
  while (!espSerial.available() && millis() - start < 500) { }// wait for tag
  if (!espSerial.available()) return;  // timeout -> exit safely

  uint8_t tag = espSerial.read();

  // --- SENSOR STRUCT (unchanged) ---
  if (tag == 0x01) {
    while (espSerial.available() < sizeof(incomingData)) {}
    espSerial.readBytes((char*)&incomingData, sizeof(incomingData));
      newSensorData = true;
      updateMenuDisplay();

    Serial.println("Arduino: Got sensor struct");
    Serial.print("Body Temp: ");     Serial.println(incomingData.bodyTemp / 100.0, 2);
    Serial.print("Ambient Temp: ");  Serial.println(incomingData.ambientTemp / 100.0, 2);
    Serial.print("Heart Rate: ");    Serial.println(incomingData.heartRate);
    Serial.print("Oxygen Level: ");  Serial.println(incomingData.oxygenLevel);
    Serial.print("Battery Level: "); Serial.println(incomingData.batteryLevel);
    Serial.print("Battery Voltage: "); Serial.println(incomingData.batteryVolt / 10.0, 1);
    Serial.println("----------------------");
  }

  // --- CMD HANDLING (rewritten same as working example) ---
  else if (tag == 0x02) {
    String cmd = espSerial.readStringUntil('\n');
    cmd.trim();
    Serial.println("CMD received: " + cmd);

    // --- Split command into 3 parts ---
    int firstSpace = cmd.indexOf(' ');
    int secondSpace = cmd.indexOf(' ', firstSpace + 1);
    if (firstSpace == -1 || secondSpace == -1) {
      Serial.println("Invalid CMD format");
      return;
    }

    String mode = cmd.substring(0, firstSpace);
    String type = cmd.substring(firstSpace + 1, secondSpace);
    String action = cmd.substring(secondSpace + 1);

    mode.trim(); type.trim(); action.trim();

    // --- Execute CMD ---
    if (mode == "Manual") {
      if (type == "light") {
        if (action == "true")startStopLight (1);
        else if (action == "false") startStopLight (0);
      }else if (type == "music") {
        if (action == "0") stopPlayback();
        else if (action == "1") playSong(0);
        else if (action == "2") playSong(1);
        else if (action == "3") playSong(2);
      }else if (type == "swinging") {
        if (action == "true") startStopMotor(1);
        else if (action == "false") startStopMotor(0);
      } 
      else if (type == "autoMode") {
        if (action == "true") startStopAutoMode(1); 
        else if (action == "false") startStopAutoMode(0);
      }

    } else if (mode == "Auto") {

      if (type == "light") {
        if (action == "true") {Automode_light_value = 1;sendStatusToESP("autoModeSettings_light_status", "true");}
        else if (action == "false") {Automode_light_value = 0;sendStatusToESP("autoModeSettings_light_status", "false");}

      } else if (type == "music") {
        if (action == "0") {Automode_music_value=-1;sendStatusToESP("autoModeSettings_music_status", "0");}
        else if (action == "1") {Automode_music_value=0;sendStatusToESP("autoModeSettings_music_status", "1");}
        else if (action == "2") {Automode_music_value=1;sendStatusToESP("autoModeSettings_music_status", "2");}
        else if (action == "3") {Automode_music_value=2;sendStatusToESP("autoModeSettings_music_status", "3");}

      } else if (type == "swinging") {
        if (action == "true") {Automode_swinging_value=1;sendStatusToESP("autoModeSettings_swinging_status", "true");}
        else if (action == "false") {Automode_swinging_value=0;sendStatusToESP("autoModeSettings_swinging_status", "false");}
      }
    }


  }
}
void sendStatusToESP(String name, String value) {
  // --- Start byte and tag ---
  espSerial.write(0xAA);   // Start byte
  espSerial.write(0x03);   // STATUS tag

  // --- Send status string ---
  String status = name + " " + value;
  status.trim();            // remove extra spaces if any
  espSerial.println(status); // newline ends frame

  // --- Debug output ---
  Serial.print("Arduino -> Sent STATUS: ");
  Serial.println(status);
}

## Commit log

2025-04-30 New files
    [components and prices.xlsx]
2025-05-01 Updating my files (report)
    [components and prices.xlsx]
2025-05-03 Designs and New report version
    [Baby Monitor 2v2 v6.stl, Crib-BallBearing-Connector-5-final-test.STL, Motor Holder v3.stl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]
2025-12-27 Version 2 of the proect
    [Baby Monitor 2v2 v6.stl, Crib-BallBearing-Connector-5-final-test.STL, Motor Holder v3.stl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]
